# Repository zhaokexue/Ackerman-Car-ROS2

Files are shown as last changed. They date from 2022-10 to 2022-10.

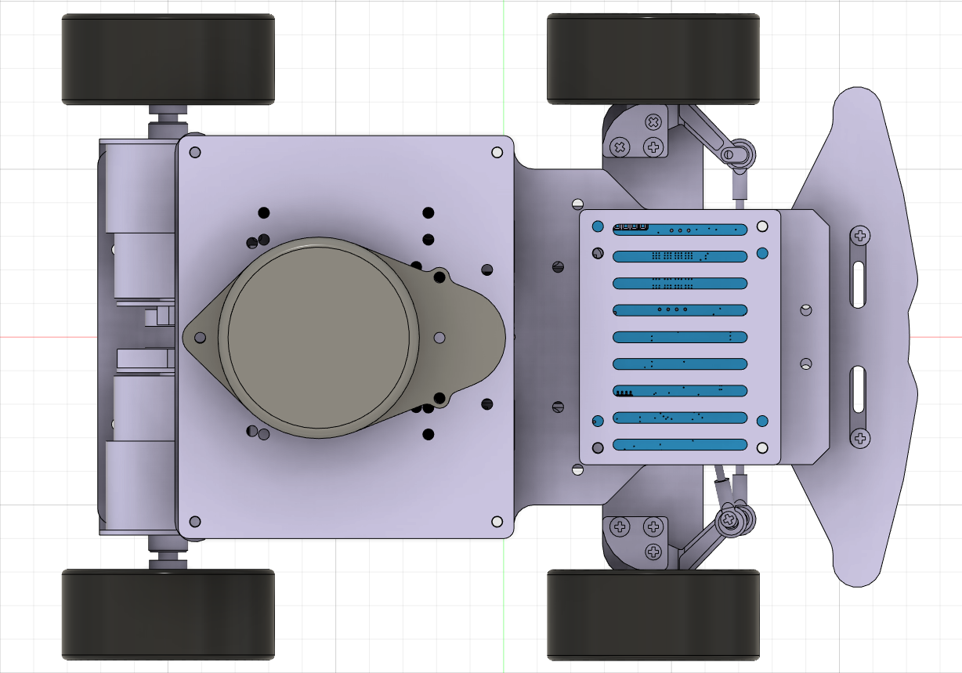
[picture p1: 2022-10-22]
1.阿克曼小车机械模型文件/屏幕截图 2022-10-22 131813.png

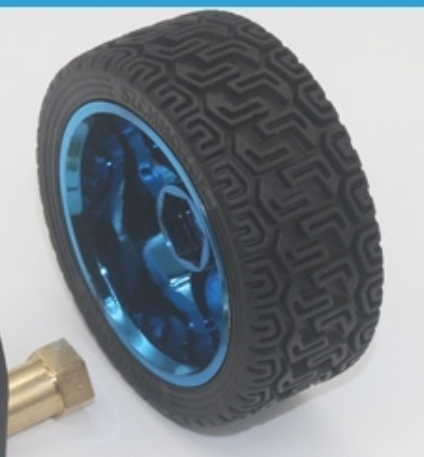
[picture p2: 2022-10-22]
3.搭建阿克曼小车材料准备/3.部分模块型号与图例/对应图片/12.png

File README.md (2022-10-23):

# ROS2阿克曼开发平台开源方案介绍

## 0、前言

### 0.1、项目背景：

为了满足更多的同学可以**快速**、**低成本**、**高兼容性**的搭建自己的阿克曼ROS2开发平台，所以出现本开源项目。

> 温馨提示：本次开源的硬件和软件是完全兼容差速和阿克曼方案的，也就是说你如果要做差速，更改机械部分之后，只需要改极少的配置文件就可以做到兼容。

开源项目发布方：**公众号：小白学移动机器人**

开源项目的内容：机械模型、底层驱动板PCB、底层驱动程序、ROS2部分功能包（启动功能包，描述功能包）等等

开源项目github地址获取：在公众号小白学移动机器人，发送：**ROS2阿克曼**，即可获取。

项目文件结构如下：



### 0.2、开源项目的总体方案：



### 0.3、开源项目的总体架构：



###0.4、开源项目的底层控制方案：



## 1、机械模型呈现

**详见：1.阿克曼小车机械模型文件**

这里机械板材的设计做了高兼容性：

> 1. 核心板安装兼容：树莓派、香橙派3LTS、jetson nano
> 2. 雷达兼容：RPLIDAR A1M8、乐动LD14、乐动LD19

左视图如下：



俯视图如下：



## 2、硬件方案介绍

详见：2.阿克曼小车硬件方案介绍

### 2.1、底层驱动板

**功能模块设计如下：**



**主控电路板PCB如下：**



**12V-5V 5A 电源板如下：**



### 2.2、核心板（香橙派3LTS）

开发板功能如下图：详见：官网：http://www.orangepi.cn/



## 3、底层驱动程序工程文件

详见：4.底层驱动程序工程文件

> 程序很简单，需要的同学可以自己看一下。
>
> 如果仍存在问题，可以参考我的系列博客文章解答你的问题。
>
> 博客链接：https://blog.csdn.net/zhao_ke_xue/article/details/108138981

博客详细的讲解的每一个控制模块的内容，如下所示：



**部分主流程代码如下：**

```c
#include "sys.h"

/*===================================================================
程序功能：ROS小车底层代码（全部） 差速底盘和阿克曼底盘通用
程序编写：公众号：小白学移动机器人
其他    ：如果对代码有任何疑问，可以私信小编，一定会回复的。
=====================================================================
------------------关注公众号，获得更多有趣的分享---------------------
===================================================================*/
int main(void)
{ 
	//发送计数
	char sendCount=0;
	
	GPIO_PinRemapConfig(GPIO_Remap_SWJ_Disable,ENABLE);
	GPIO_PinRemapConfig(GPIO_Remap_SWJ_JTAGDisable,ENABLE);//禁用JTAG 启用 SWD
	
	MY_NVIC_PriorityGroupConfig(2);	//=====设置中断分组
	
	delay_init();	    	        //=====延时函数初始化
	LED_Init();                     //=====LED初始化    程序灯	
	BEEP_Init();                    //=====蜂鸣器初始化，异常报警
	
	usart1_init(115200);	        //=====串口1初始化  树莓派通信
	usart3_init(115200);            //=====串口3初始化  蓝牙，控制和调试

	IIC_Init();                     //=====IIC初始化    读取MPU6050数据
	MPU6050_initialize();           //=====MPU6050初始化	
	DMP_Init();                     //=====初始化DMP 

	Encoder_Init_TIM3();            //=====初始化右轮编码器接口
	Encoder_Init_TIM4();            //=====初始化左轮编码器接口
	
	MY_ADC_Init();                  //=====adc初始化    电池电量检测
	
	Motor_PWM_Init(7200-1, 1-1);    //=====初始化PWM 10KHZ(AT8870)，用于驱动电机 
	Steer_PWM_Init(60000-1, 24-1);  //=====初始化PWM 50HZ，用于驱动舵机

	PID_Init();                     //=====PID初始化
	
	MBOT_EXTI_Init();               //=====MPU6050 5ms定时中断初始化

	while(1)
	{
		//给树莓派发送速度，角度,这里速度已经乘以1000,角度(0.0-359.0)乘以50
		if(sendCount==0)//发送  14.4ms  发送一次数据 70Hz 左右
		{
			//发送需要一定的延时
			usartSendData(USART1,(short)leftSpeedNow,(short)rightSpeedNow,(short)(yaw*50),sendCtrlFlag);  //1ms
			//蓝牙调试时用，不调试注释
			// pcShow();                                                           //2.2ms单个float数据
			sendCount++;
		}
		else
		{
			sendCount++;
			if(sendCount==25)
				sendCount=0;
		}
		//获取角度		
		getAngle(&yaw,&yaw_acc_error);                                                     
	} 
}

//中断服务函数
void USART1_IRQHandler()
{
	if(USART_GetITStatus(USART1, USART_IT_RXNE) != RESET)
 	 {
		 USART_ClearITPendingBit(USART1,USART_IT_RXNE);//首先清除中断标志位
		 usartReceiveOneData(USART1,&leftSpeedSet,&rightSpeedSet,&frontAngleSet,&receCtrlFlag);
	 }
}
```

**中断主流程代码如下：**

```c
/**************************************************************************
函数功能：所有的控制代码都在这里面
          5ms定时中断由MPU6050的INT引脚触发		
**************************************************************************/
void EXTI9_5_IRQHandler(void) 
{                                                         
	EXTI_ClearITPendingBit(EXTI_Line8);                             //===清除LINE8线路挂起位		
	
	Led_Flash(200);                                                 //===LED闪烁，证明程序正常运行	
	
	yaw_acc_error += FIVE_MS_ERROR;								    //===yaw漂移误差累加
	
	Get_battery_volt_average(&Voltage,100);		                    //===电池电压测量，单位mv，100次取一次平均
	
	Get_Motor_Speed(&leftSpeedNow,&rightSpeedNow);                  //===获取左右轮子真实速度
	
	pid_Task_Letf.speedSet  = leftSpeedSet;	                        //===给速度设定值和实时值赋值
	pid_Task_Right.speedSet = rightSpeedSet;
	pid_Task_Letf.speedNow  = leftSpeedNow;
	pid_Task_Right.speedNow = rightSpeedNow;
	
	Pid_Ctrl(&motorLeft,&motorRight);                               //===执行PID控制函数
	Steer_Ctrl(frontAngleSet,&motorFrontSteer);                     //===执行舵机，差速小车无需修改完全兼容

	if(Turn_Off(Voltage) == 0)                                      //===如果电量异常低
	{	
		BEEP_Disable();                                             //===正常情况，蜂鸣器失能 
		Set_Pwm(motorLeft,motorRight,motorFrontSteer);              //===赋值给PWM寄存器 		
	} 	  
	else
	{
		BEEP_Flash(20);                                            	//===电量报警
	}
} 
```

## 4、机械模型转URDF模型文件

详见：5.机械模型转URDF模型文件介绍

**rviz显示如下图：**



## 5、阿克曼结构运动模型详解

详见：6.阿克曼结构运动模型详解





## 6、阿克曼ROS2相关功能包

详见：7.ROS2相应功能包

```bash
.
└── src
    ├── mbot_bringup        # 机器人启动功能包 和 底层单片机通信、发布里程计、tf、订阅控制话题
    ├── mbot_description    # 机器人描述功能包，机械模型转的urdf
    └── sllidar_ros2-humble # RPLIDAR A1M8 的ROS2驱动
```

程序很简单，需要的同学可以自己看一下。

## 7、系统配置以及功能包启动说明

详见：8.系统配置以及功能包启动



##  8、总结

如果你觉得本开源项目还不错，可以积极的分享到你的同学、朋友。

**如果你感觉，我的文章比较适合你，关注我，点个赞，给你不一样的惊喜。**





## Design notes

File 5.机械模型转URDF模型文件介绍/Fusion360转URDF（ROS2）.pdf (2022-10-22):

# Fusion360转URDF（ROS2）

# 1、建模部分

# 1.1、熟悉fusion的基本操作

## 熟练使用命名视图

## 熟练使用草图工具

## 熟练使用移动工具

## 熟练使用测量工具

## 快捷键：

## m：移动选中的实体 i：测量长度 e：拉伸选中的面 f：倒圆角（选中的边或者面）

## 建模步骤：草图 - > 实体创建（相关操作）-> 从实体转换零部件 -> 装配（建立零部件之间的链接关系）

# 1.2、转换URDF对模型的要求

## 1. 模型尽可能简单，若是机械模型，先把主体部分合并为一个大的实体 2. 装配时建立零部件链接关系要正确，不能使用快速链接

# 1.3、建模的步骤

## 建模步骤：草图 - > 实体创建（相关操作）-> 从实体转换零部件 -> 装配（建立零部件之间的链接关系）

## 草图创建：

## 1. 选择创建的面 2. 通过任意线、矩形框、圆形框、镜像等工具，设计草图 3. 完成草图

## 实体的创建：

## 1. 选择需要操作的草图的面 2. 可以通过拉伸、旋转等操作对选择的面进行操作 3. 点击确定，即可生成一个新的实体

## 零部件的创建：

## 1. 从实体创建零部件 2. 实体消失，生成零部件 3. 修改零部件名称；名称必须是英文或者拼音

## 反复以上操作完成所有零部件的创建

## 创建零部件之间的链接关系：

## 1. 快捷键j

## 2. 只允许使用链接，不能使用快速链接

## 链接关系创建完成后，保存，文件结构如下图所示。

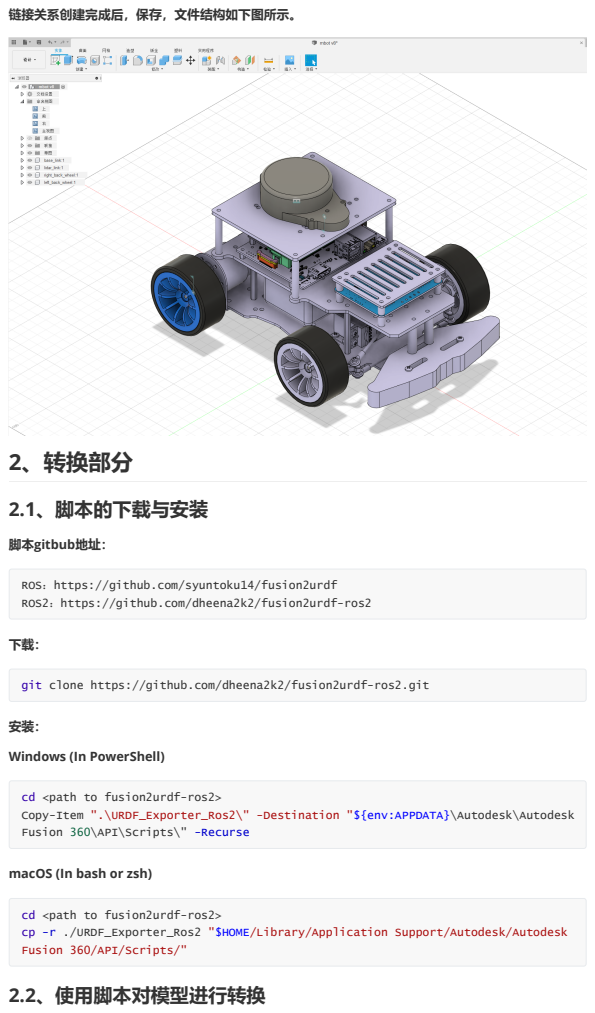
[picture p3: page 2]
2、转换部分; 2.1、脚本的下载与安装; 脚本gitbub地址：

ROS：https://github.com/syuntoku14/fusion2urdf
ROS2：https://github.com/dheena2k2/fusion2urdf-ros2

git clone https://github.com/dheena2k2/fusion2urdf-ros2.git

Windows (In PowerShell)

cd <path to fusion2urdf-ros2>
Copy-Item ".\URDF_Exporter_Ros2\" -Destination "${env:APPDATA}\Autodesk\Autodesk
Fusion 360\API\Scripts\" -Recurse

macOS (In bash or zsh)

cp -r ./URDF_Exporter_Ros2 "$HOME/Library/Application Support/Autodesk/Autodesk
Fusion 360/API/Scripts/"
2.2、使用脚本对模型进行转换

## 打开fusion360，点击实用程序、点击附加模块、选择我的脚本 URDF_Exporter_Ros2，最后点击运 行，选择生成文件夹。

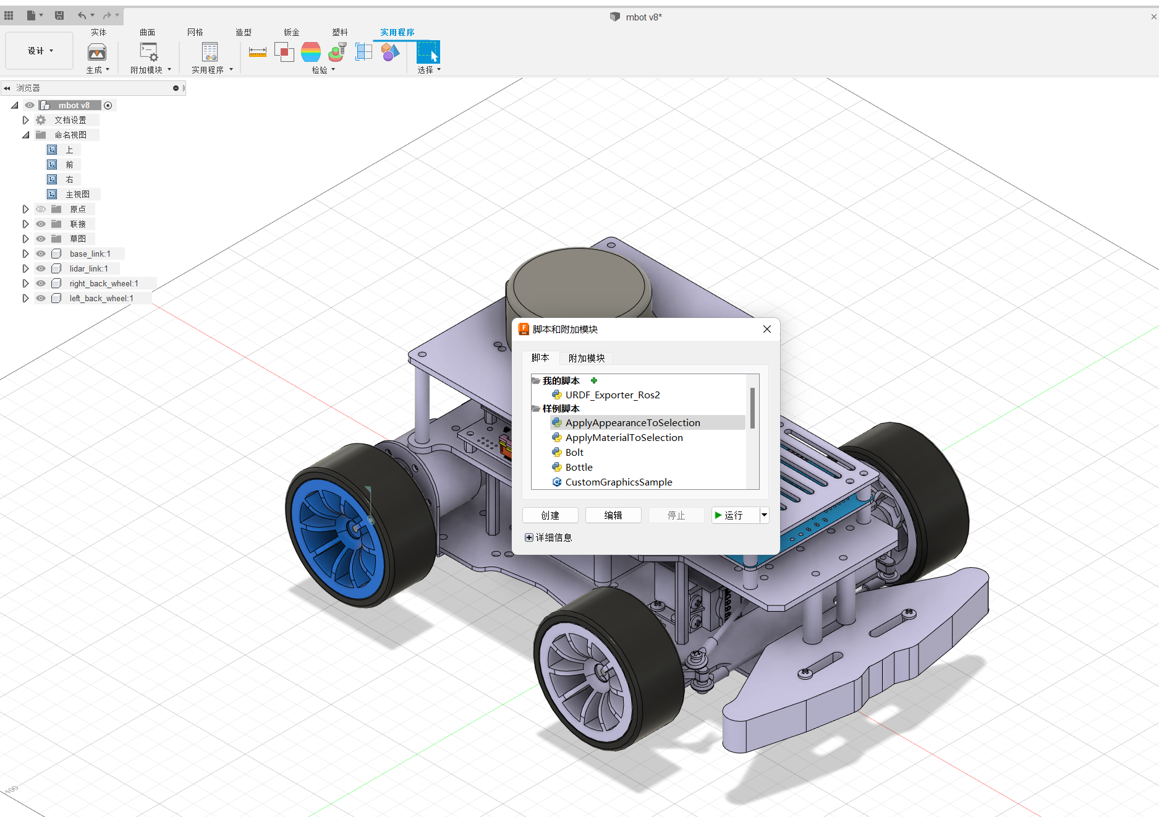
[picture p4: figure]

# 2.3、在ROS2使用转换后的ROS机器人描述功能包

## 首先，将生成的机器人描述功能包拷贝到ROS2的工作空间的src目录下

## ROS2环境与相关软件包安装：

## 编译与刷新环境：

## rviz显示运行：

sudo apt-get install libboost-dev #orangepi 没有安装此库 后期编译代码使用

ros2 launch mbot_description display.launch.py

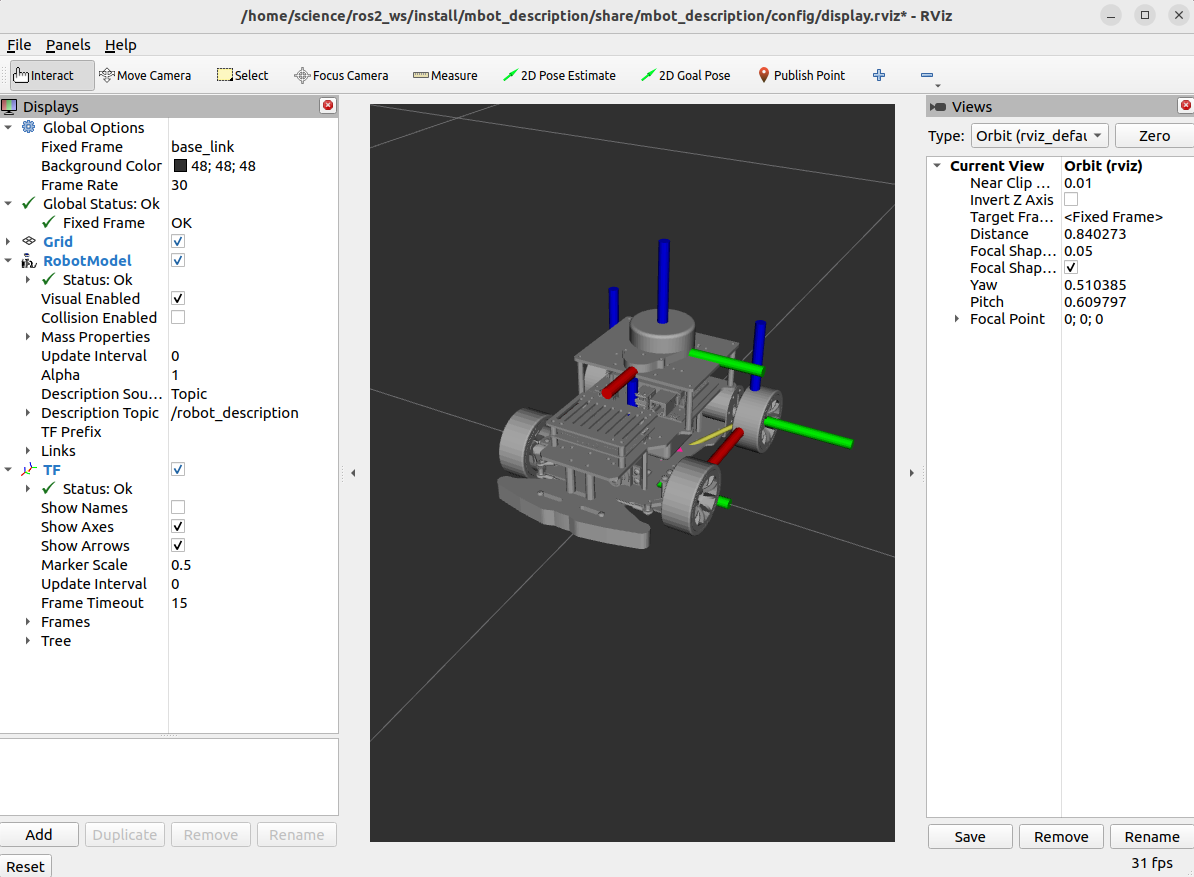
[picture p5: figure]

## 这样，通过fusion360建模软件就完成机器人描述文件的导出了。

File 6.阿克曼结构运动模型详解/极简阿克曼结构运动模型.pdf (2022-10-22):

# 极简版搭建阿克曼ROS小车相关

0、前言

## 本篇文章仅是对常见阿克曼ROS小车的极简分析，并提供代码。主要是方便读者自己搭建阿克曼小车时 理解使用。

## 这里仅针对《舵机控制前轮转向+后轮主动差速》的方式，如下图所示：

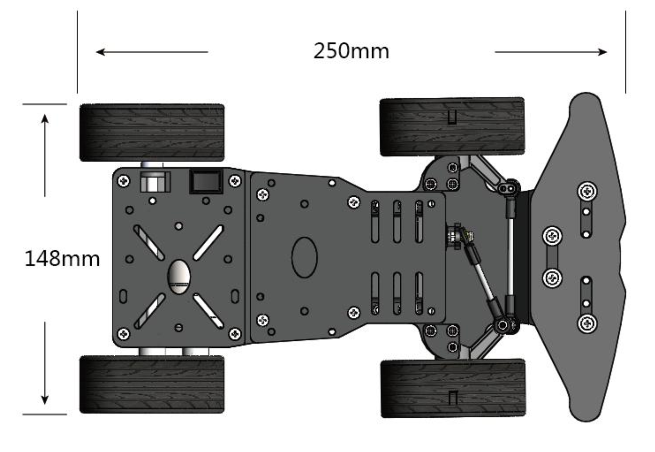
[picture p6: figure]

## 图片来源：百度图片

# 舵机转向机构简单示意图

## 舵机完成前轮的转向控制，简单示意图如下：

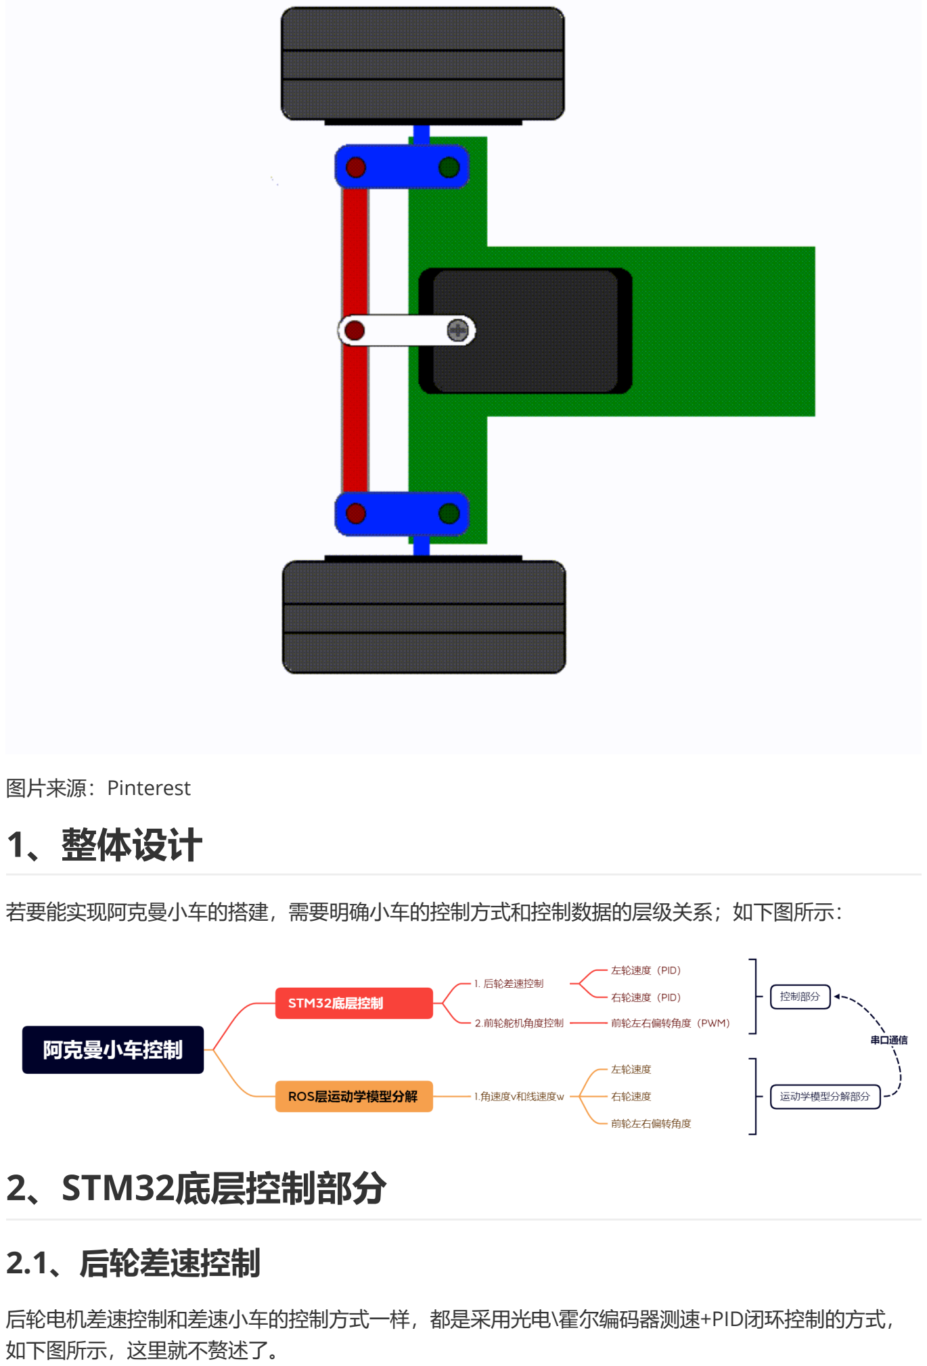
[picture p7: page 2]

## 图片来源：Pinterest

# 1、整体设计

## 若要能实现阿克曼小车的搭建，需要明确小车的控制方式和控制数据的层级关系；如下图所示：

# 2、STM32底层控制部分

# 2.1、后轮差速控制

## 后轮电机差速控制和差速小车的控制方式一样，都是采用光电\霍尔编码器测速+PID闭环控制的方式， 如下图所示，这里就不赘述了。

## 需要了解的朋友可以看之前的文章，链接如下：

# 2.2、前轮舵机角度控制

# 2.2.1、舵机选型：

## 这里主要使用如下两种模拟舵机，常见模拟舵机都可以。

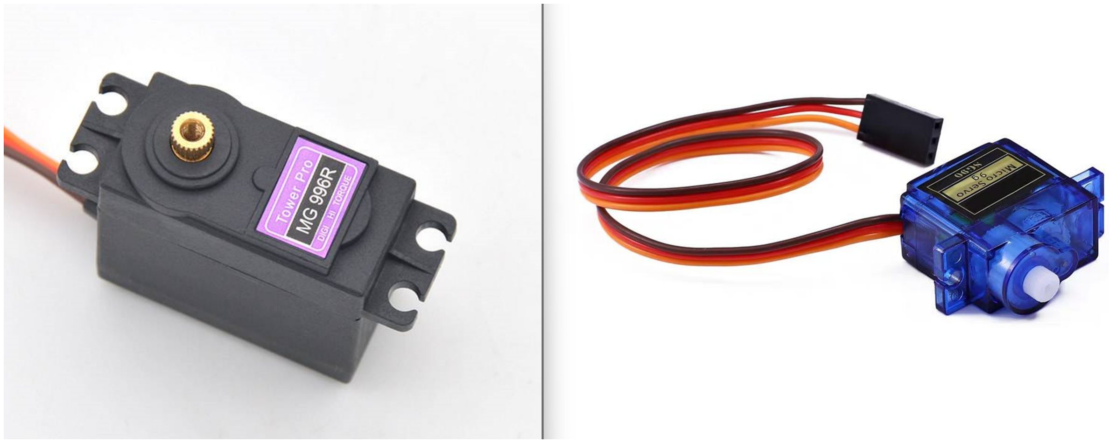
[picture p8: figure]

## 图片来源：百度图片

# 2.2.2、舵机控制原理：

## 舵机是一种位置伺服驱动器，是一种带有输出轴的小装置。当我们向伺服器发送一个控制信号时，输出 轴就可以转到特定的位置。只要在控制信号持续不变，伺服机构就会保持相对的角度位置不变。如果控 制信号发生变化，输出轴的位置也会相应发生变化。舵机的控制大部分都是通过PWM信号控制的。

# 2.2.3、单片机控制舵机：

## 模拟舵机控制一般需要20ms左右时基脉冲， 该脉冲高电平部分一般为0.5ms-2.5ms范围内角度控制脉 冲部分， 总间隔为2ms。 以180度角度伺服为例， 对应控制关系如下 ：

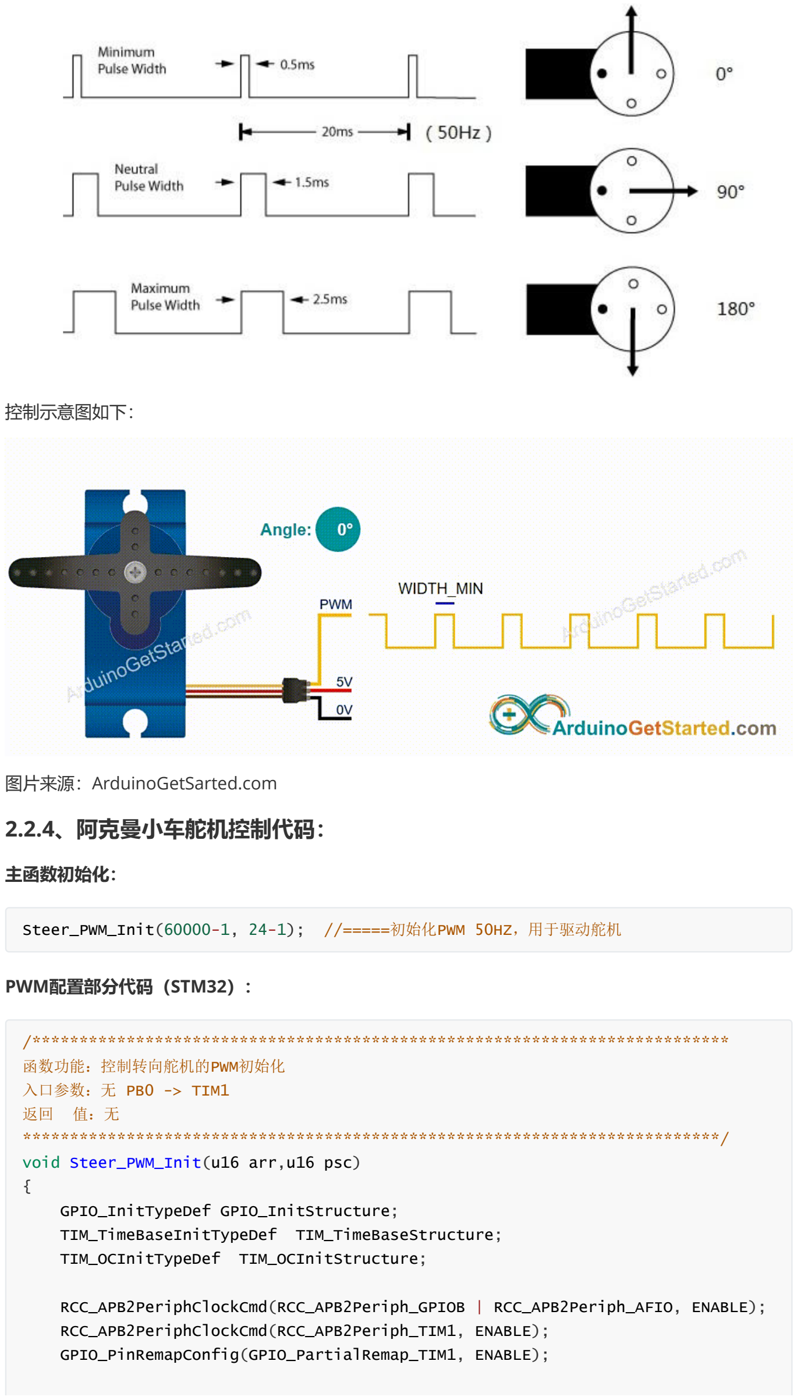
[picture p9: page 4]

## 控制示意图如下：

## 图片来源：ArduinoGetSarted.com

# 2.2.4、阿克曼小车舵机控制代码：

## 主函数初始化：

## PWM配置部分代码（STM32）：

Steer_PWM_Init(60000-1, 24-1); //=====初始化PWM 50HZ，用于驱动舵机

/************************************************************************** 函数功能：控制转向舵机的PWM初始化
入口参数：无 PB0 -> TIM1
返回 值：无
**************************************************************************/ void Steer_PWM_Init(u16 arr,u16 psc)
{
| GPIO_InitTypeDef GPIO_InitStructure; TIM_TimeBaseInitTypeDef TIM_TimeBaseStructure; TIM_OCInitTypeDef TIM_OCInitStructure;
| RCC_APB2PeriphClockCmd(RCC_APB2Periph_GPIOB | RCC_APB2Periph_AFIO, ENABLE); RCC_APB2PeriphClockCmd(RCC_APB2Periph_TIM1, ENABLE); GPIO_PinRemapConfig(GPIO_PartialRemap_TIM1, ENABLE);

## 前轮转向控制角度和PWM的转换函数：

GPIO_InitStructure.GPIO_Pin = GPIO_Pin_0; GPIO_InitStructure.GPIO_Mode = GPIO_Mode_AF_PP; GPIO_InitStructure.GPIO_Speed = GPIO_Speed_50MHz; GPIO_Init(GPIOB, &GPIO_InitStructure);

TIM_TimeBaseStructure.TIM_Period = arr; TIM_TimeBaseStructure.TIM_Prescaler = psc; TIM_TimeBaseStructure.TIM_ClockDivision = TIM_CKD_DIV1; TIM_TimeBaseStructure.TIM_CounterMode = TIM_CounterMode_Up; TIM_TimeBaseInit(TIM1, &TIM_TimeBaseStructure);

TIM_OCInitStructure.TIM_OCMode = TIM_OCMode_PWM1;
// * TIM1_CH2
// TIM_OCInitStructure.TIM_OutputState = TIM_OutputState_Enable; // TIM_OCInitStructure.TIM_Pulse = 0;
// TIM_OCInitStructure.TIM_OCPolarity = TIM_OCPolarity_High;
// * TIM1_CH2N
TIM_OCInitStructure.TIM_OutputNState = TIM_OutputNState_Enable; TIM_OCInitStructure.TIM_Pulse = 0; TIM_OCInitStructure.TIM_OCNPolarity = TIM_OCNPolarity_Low;
TIM_OC2Init(TIM1, &TIM_OCInitStructure); | //TIM_OC2
TIM_OC2PreloadConfig(TIM1, TIM_OCPreload_Enable);
TIM_ARRPreloadConfig(TIM1, ENABLE); | //使能TIMx在ARR上的预装载
寄存器
TIM_CtrlPWMOutputs(TIM1, ENABLE); | //MOE 主输出使能 | 高级定
时器使用

TIM_Cmd(TIM1, ENABLE);
}

//舵机PWM变量，初始安装为90度，注意机械安装时，要先转到90度再安装舵盘 int motorFrontSteer = 4500; // (60000 / 20ms) * 1.5ms = 4500 90度

//舵机控制角度的设定值
int frontAngleSet = 0;

// 物理结构限幅，舵机角度限幅
#define MAX_FRONT_ANGLE_SET (50)

/************************************************************************** 函数功能：舵机角度控制处理（SG90）角度线性变化
入口参数：ros端设定转向角度，需要给舵机的pwm，此处可根据不同的舵机自行更改
分辨率：1度 --> ((2.5ms - 0.5ms) / 180度) * (60000 / 20ms) = 33.3
0.5ms ------------------ 0度
1.5ms ------------------ 90度
2.5ms ------------------ 180度
返回 值：无
**************************************************************************/ void Steer_Ctrl(int frontAngleSet,int *motorFrontSteer)
{
| // 物理结构限幅 if(frontAngleSet > MAX_FRONT_ANGLE_SET)

{

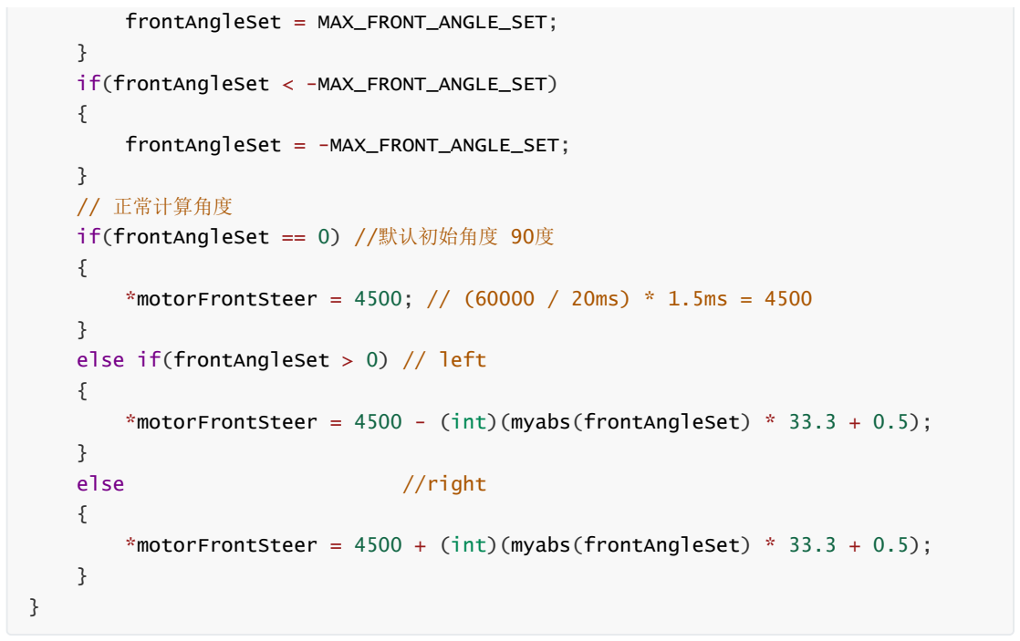
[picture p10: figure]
frontAngleSet = MAX_FRONT_ANGLE_SET;; } if(frontAngleSet < -MAX_FRONT_ANGLE_SET); frontAngleSet = -MAX_FRONT_ANGLE_SET;; } // 正常计算角度; if(frontAngleSet == 0) //默认初始角度 90度; } else if(frontAngleSet > 0) // left; else; //right

## 通过上面转换函数 Steer_Ctrl，我们可以将前轮转向角度准换为具体的PWM数值，剩下的部分就是 PWM设置的问题了，大家这么聪明，肯定不用我多说了。

大家是不是觉得阿克曼小车的底层控制部分 So Easy.

# 3、极简版阿克曼结构运动学模型

# 3.1、模型示意图介绍：

## 阿克曼底盘的运动学模型是一个全驱动模型，简化模型示意图如下：

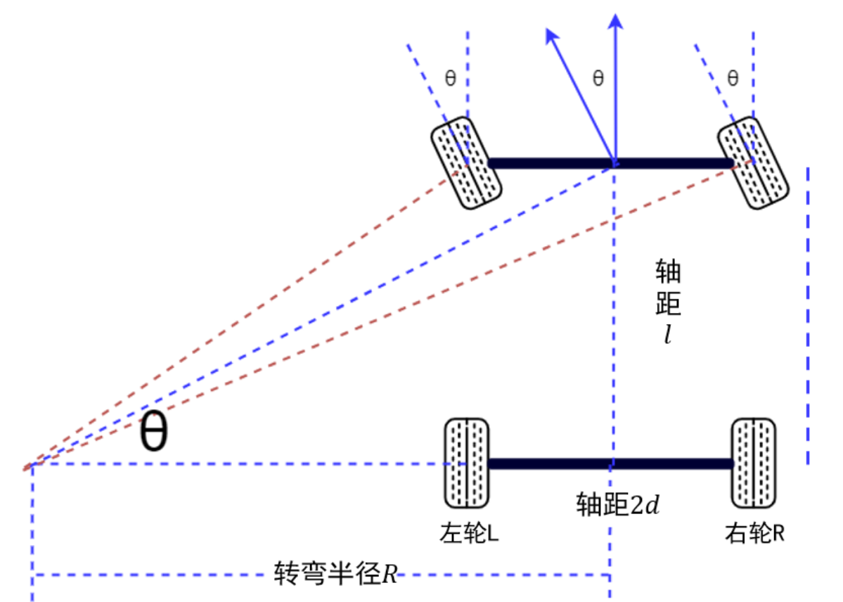
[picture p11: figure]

## 图片来源：CSDN：Jason.Li_0012 (https://blog.csdn.net/weixin_45929038)

*motorFrontSteer = 4500; // (60000 / 20ms) * 1.5ms = 4500

*motorFrontSteer = 4500 - (int)(myabs(frontAngleSet) * 33.3 + 0.5);

*motorFrontSteer = 4500 + (int)(myabs(frontAngleSet) * 33.3 + 0.5);

# 3.2、模型假设：

## 相对于理想的阿克曼底盘模型，这里为了简化模型，做了如下假设：

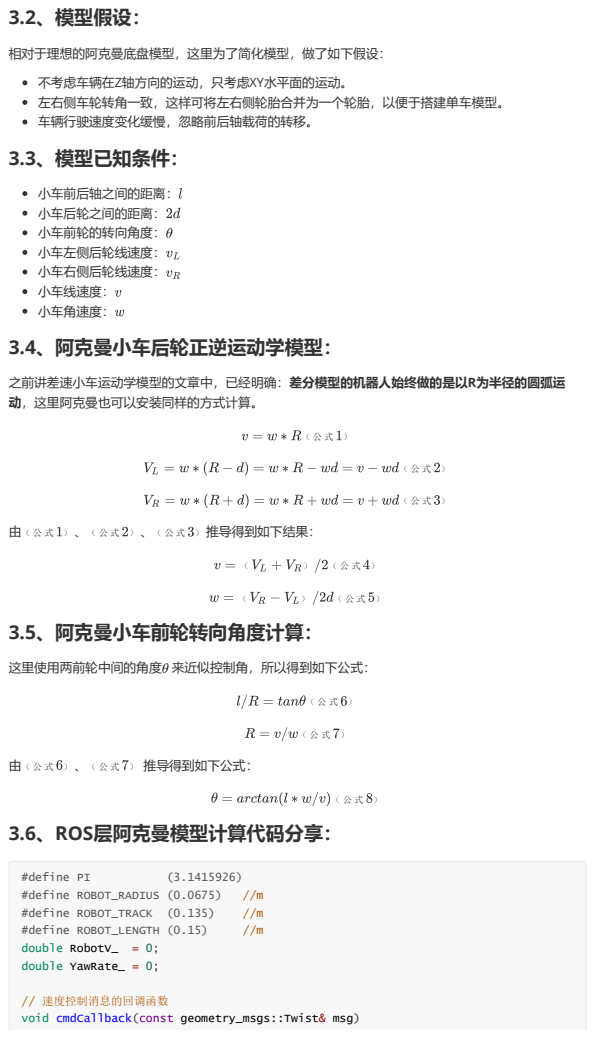
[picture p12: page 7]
小车前后轴之间的距离： 小车后轮之间的距离： 小车前轮的转向角度： 小车左侧后轮线速度： 小车右侧后轮线速度： 小车线速度： 小车角速度： 3.4、阿克曼小车后轮正逆运动学模型：; 由（ 公 式 ） 、（ 公 式 ） 、（ 公 式 ） 推导得到如下结果：; 3.5、阿克曼小车前轮转向角度计算：; 由（ 公 式 ） 、（ 公 式 ） 推导得到如下公式：; （ 公 式 ） 3.6、ROS层阿克曼模型计算代码分享：; #define PI; #define ROBOT_RADIUS (0.0675); #define ROBOT_TRACK; #define ROBOT_LENGTH (0.15); double RobotV_; double YawRate_ = 0;

不考虑车辆在Z轴方向的运动，只考虑XY水平面的运动。
左右侧车轮转角一致，这样可将左右侧轮胎合并为一个轮胎，以便于搭建单车模型。
车辆行驶速度变化缓慢，忽略前后轴载荷的转移。
3.3、模型已知条件：

之前讲差速小车运动学模型的文章中，已经明确：差分模型的机器人始终做的是以R为半径的圆弧运
动，这里阿克曼也可以安装同样的方式计算。

这里使用两前轮中间的角度 来近似控制角，所以得到如下公式：

// 速度控制消息的回调函数
void cmdCallback(const geometry_msgs::Twist& msg)

4、总结

## 如果你已经仔细的看到这里，那么恭喜你，你心中一定有了搭建阿克曼小车的控制思路了。

## 如果还没有理解，一定多看两遍。

## 偷偷的告诉大家，近期，我准备开源一整套，完整的ROS小车方案，包含差速小车和阿克曼小车，届时 将给大家提供完整上位机和下位机的代码，整套方案成本极低，千元以内。

## 下面是底层硬件方案，提前透露给大家。

{
RobotV_ | = msg.linear.x; | //m/s
YawRate_ = msg.angular.z; //rad/s
}

void Mbot::ackerCar(const double RobotV,const double YawRate) {
double r = RobotV / YawRate; // m
if(RobotV == 0) | // ackermann car can't trun rotation
{
sendLeftSpeed_ = 0;
sendRightSpeed_ = 0;
sendFrontAngle_ = 0;
}
else
if(YawRate == 0) // Pure forward/backward motion
{
sendLeftSpeed_ = (short)(RobotV * 1000.0);//mm/s sendRightSpeed_ = (short)(RobotV * 1000.0); sendFrontAngle_ = 0;
}
else | // Rotation about a point in space
{
sendLeftSpeed_ = (short)(YawRate * 1000.0 * (r - ROBOT_RADIUS));//mm/s sendRightSpeed_ = (short)(YawRate * 1000.0 * (r + ROBOT_RADIUS));

// 阿克曼约束一：后左右车轮转动需同向
if(RobotV > 0)
{
if(sendLeftSpeed_ < 0) {sendLeftSpeed_ = 0;} if(sendRightSpeed_ < 0) {sendRightSpeed_ = 0;} }
else if(RobotV < 0)
{
if(sendLeftSpeed_ > 0) {sendLeftSpeed_ = 0;}
if(sendRightSpeed_ > 0) {sendRightSpeed_ = 0;}
}
sendFrontAngle_ = atan(ROBOT_LENGTH * YawRate / RobotV ) * (180.0 / PI); // Deg
}
}

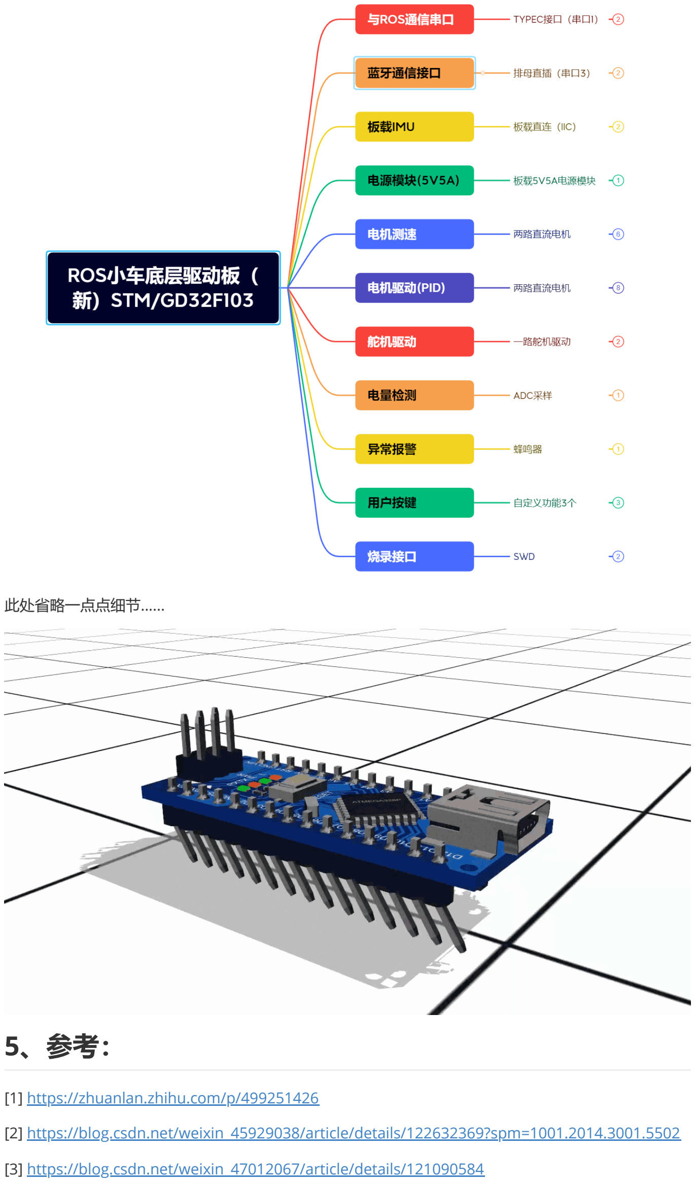
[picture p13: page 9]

此处省略一点点细节......

5、参考：

## [1] https://zhuanlan.zhihu.com/p/499251426

[2] https://blog.csdn.net/weixin_45929038/article/details/122632369?spm=1001.2014.3001.5502

## [3] https://blog.csdn.net/weixin_47012067/article/details/121090584

## [4] https://blog.csdn.net/honorzoey/article/details/113407979

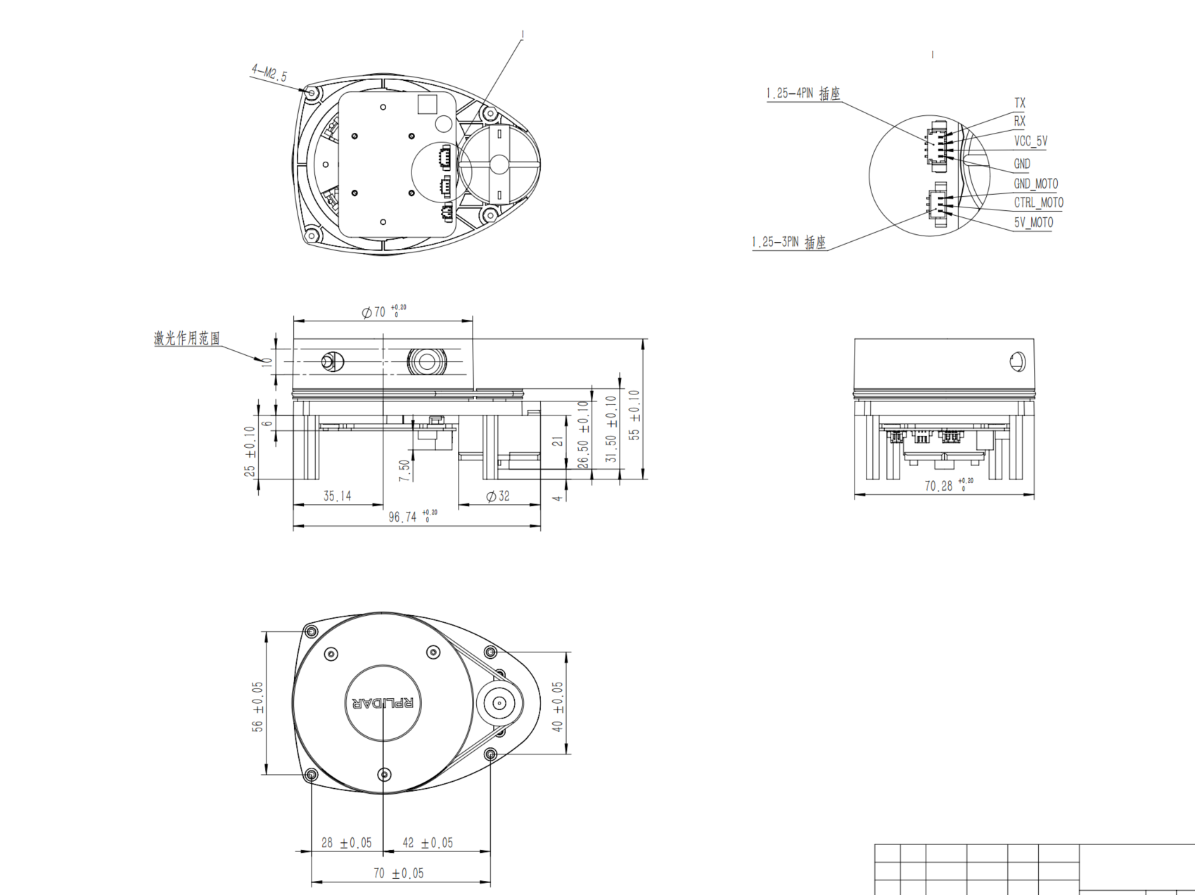
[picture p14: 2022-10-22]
2.阿克曼小车硬件方案介绍/3.RPLIADR A1M8/激光雷达-rplidar-A1M8.png

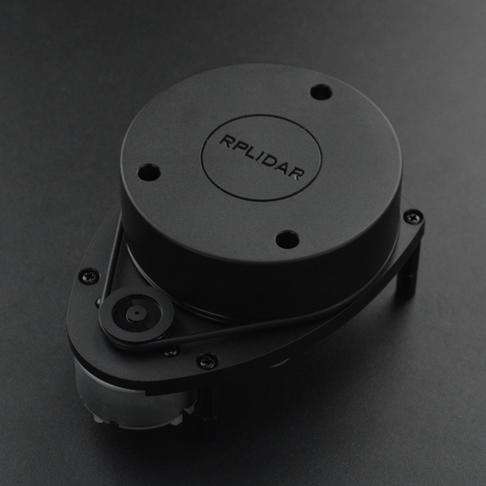
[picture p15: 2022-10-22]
2.阿克曼小车硬件方案介绍/3.RPLIADR A1M8/A1M8.jpeg

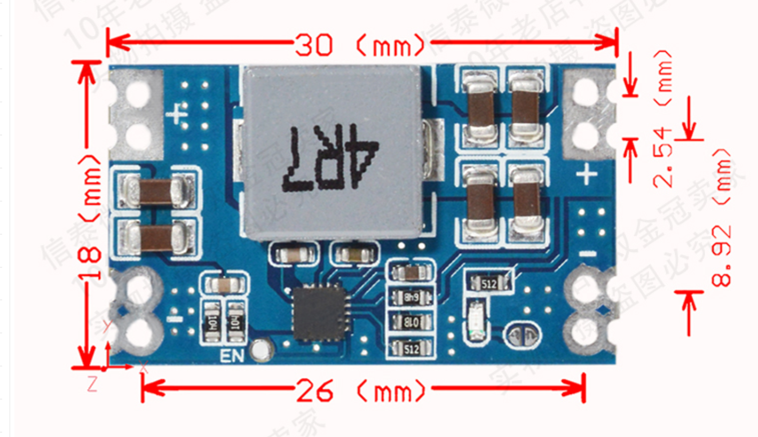
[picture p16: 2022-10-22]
2.阿克曼小车硬件方案介绍/1.STM32底层电路驱动板/3.电源板图（购买mini 560 12V-5V 5A）.png

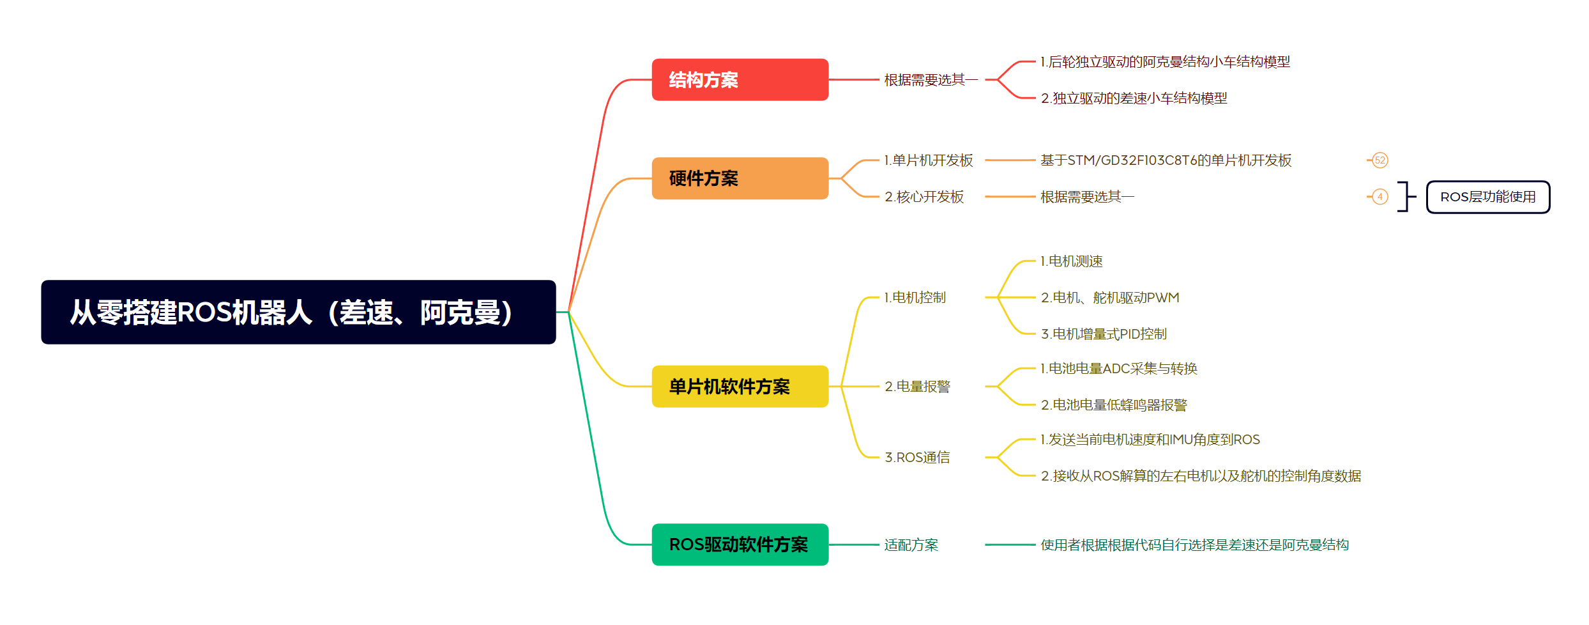
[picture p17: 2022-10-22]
0.开源项目介绍/差速/总体方案.png

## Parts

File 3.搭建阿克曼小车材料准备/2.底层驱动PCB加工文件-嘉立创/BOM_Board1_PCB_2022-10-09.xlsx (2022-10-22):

No. | Quantity | Comment | Designator | Footprint | Value | Manufacturer Part | Manufacturer | Supplier Part | Supplier
2 | 5 | 100n | C3,C21,C22,C23,C24 | C0402
3 | 7 | 0.1u | C6,C7,C12,C19,C20,C25,C33 | C0402
5 | 2 | 1u | C11,C13 | C0402
6 | 6 | 0.1u | C15,C28,C29,C30,C31,C32 | C1206
8 | 1 | 2.2n | C26 | C0805
9 | 1 | 100uF | C36 | CAP-SMD_BD8.0-L8.3-W8.3-LS9.3-FD | 100uF | RVT100UF50V67RV0040 | KNSCHA(科尼盛) | C2836439 | LCSC
10 | 2 | 22pF | C38,C39 | C0402 | 22pF | 0402CG220J500NT | FH(风华) | C1555 | LCSC
11 | 1 | 100uF | C40 | C1206 | 100uF | CL31A107MQHNNNE | SAMSUNG(三星) | C15008 | LCSC
14 | 1 | 0.35,0.75A | F1 | F0805 |  | 贴片保险丝0.05ASelf-recovery | RUILON | C30198 | LCSC
19 | 1 | 19-217/GHC-YR1S2/3T | LED1 | LED0603-R-RD |  | 19-217/GHC-YR1S2/3T | EVERLIGHT(台湾亿光) | C72043 | LCSC
20 | 1 | KT-0603R | LED2 | LED0603-R-RD |  | KT-0603R | KENTO | C2286 | LCSC
22 | 2 | 100K | R4,R15 | R0402
23 | 1 | 20K | R5 | R0402
25 | 4 | 4.7k | R12,R13,R14,R16 | R0402
27 | 1 | K2-1806SA-A3DW-04 | S1 | KEY-SMD_K2-1806SA-AXXW-XX
30 | 3 | K2-1806SA-A3DW-04 | SW1,SW2,SW3 | KEY-SMD_K2-1806SA-AXXW-XX |  | K2-1806SA-A3DW-04 | 韩国韩荣 | C2690015 | LCSC
34 | 1 | RT9013-33GB | U5 | SOT-23-5_L3.0-W1.7-P0.95-LS2.8-BR |  | RT9013-33GB | RICHTEK | C47773 | LCSC
40 | 1 | 8MHz | X1 | CRYSTAL-SMD_L5.0-W3.2 | 8MHz | X50328MSB2GI | YXC扬兴科技 | C115962 | LCSC
41 | 1 | 1k | R9 | R0402
42 | 4 | 10k | R6,R22,R23,R24 | R0402
43 | 1 | 510 | R8 | R0402
46 | 1 | 47 | R17 | R0402
47 | 2 | 0.2 | R25,R26 | R0805
48 | 1 | MMS8050-H-TP | Q3 | SOT-23-3_L2.9-W1.3-P1.90-LS2.4-BR
51 | 1 | TYPEC-307DSW-ACP16 | USB1 | USB-C-SMD_TYPEC-307DSW-ACP16
52 | 1 | C2765187 | USB3 | MICRO-USB-SMD_MICRO-5.9ZB5.0-040
53 | 1 | 1.5-4P卧贴 | H5 | CONN-SMD_ZH1.5-4P_SMD
54 | 1 | CH340N | U4 | SOP-8_L5.0-W4.0-P1.27-LS6.0-BL
55 | 1 | GD32F103C8T6 | U3 | TQFP-48_L7.0-W7.0-P0.50-LS9.0-BL
56 | 2 | AT8870 | U10、U11 | SOP-8_L4.9-W3.9-P1.27-LS6.0-BL-EP

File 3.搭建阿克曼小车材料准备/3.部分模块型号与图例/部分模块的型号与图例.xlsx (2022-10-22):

序号 | 名称 | 型号 | 个数 | 淘宝链接
1 | SD卡 | 闪迪8\16G高速卡 | 1 | https://item.taobao.com/item.htm?spm=a1z09.2.0.0.5a282e8d9ynWcl&id=648729260877&_u=n27e0jt0e6f9
2 | 电池套装 | 12V电池充电器套装 | 1 | https://item.taobao.com/item.htm?spm=a1z09.2.0.0.5a282e8d9ynWcl&id=624879497879&_u=n27e0jt0d620
3 | XT30U电池插头连接线 | 母头10cm | 1 | https://item.taobao.com/item.htm?spm=a1z09.2.0.0.5a282e8d9ynWcl&id=598407253999&_u=n27e0jt0d5d5
4 | USB转安卓micro | 15cm 数据线 | 1 | https://detail.tmall.com/item.htm?_u=n27e0jt0f0cd&id=646439713283&spm=a1z09.2.0.0.5a282e8d9ynWcl
5 | USB转TYPEC | 25cm 数据线 | 1 | https://detail.tmall.com/item.htm?_u=n27e0jt09f1e&id=666724356790&spm=a1z09.2.0.0.5a282e8d9ynWcl
6 | 安卓micro转TYPEC | 25cm 数据线 | 1 | https://item.taobao.com/item.htm?spm=a1z09.2.0.0.5a282e8d9ynWcl&id=652595705306&_u=n27e0jt0b8d3
7 | 底层板需要的一些配件 | 底层驱动板需要的 | 1 | https://item.taobao.com/item.htm?spm=a1z09.2.0.0.5a282e8d9ynWcl&id=635227665423&_u=n27e0jt04848
8 | 亚克力加工 |  | 1 | https://item.taobao.com/item.htm?spm=a1z09.2.0.0.5a282e8d9ynWcl&id=650568186676&_u=n27e0jt0e97c
9 | 舵机 | MG995 | 1 | https://item.taobao.com/item.htm?spm=a1z09.2.0.0.5a282e8d9ynWcl&id=573547711366&_u=n27e0jt045a3
10 | 舵机座 | 配件MG995 | 1 | https://item.taobao.com/item.htm?spm=a1z09.2.0.0.5a282e8d9ynWcl&id=603661493122&_u=n27e0jt054bd
11 | 前轮舵机转向结构 |  | 1 | https://item.taobao.com/item.htm?spm=a1z09.2.0.0.5a282e8d9ynWcl&id=656136453494&_u=n27e0jt0a753
12 | 智能小车轮子 | 防滑车轮 | 2 | https://item.taobao.com/item.htm?spm=a1z09.2.0.0.5a282e8d9ynWcl&id=656136453494&_u=n27e0jt0a753
13 | 12V直流减速电机 | 12V直流减速电机套装 | 2 | https://item.taobao.com/item.htm?spm=a1z0d.6639537/tb.1997196601.312.48c77484EUyhPv&id=584588142034
14 | 香橙派 | 3LTS | 1 | https://item.taobao.com/item.htm?spm=a1z0d.6639537/tb.1997196601.389.48c77484EUyhPv&id=665424457812
15 | 电机链接线 | H2.54排线-6p-25cm | 2 | https://item.taobao.com/item.htm?spm=a1z10.3-c-s.w4002-21223910208.14.2a696a4bWT919G&id=565759164574

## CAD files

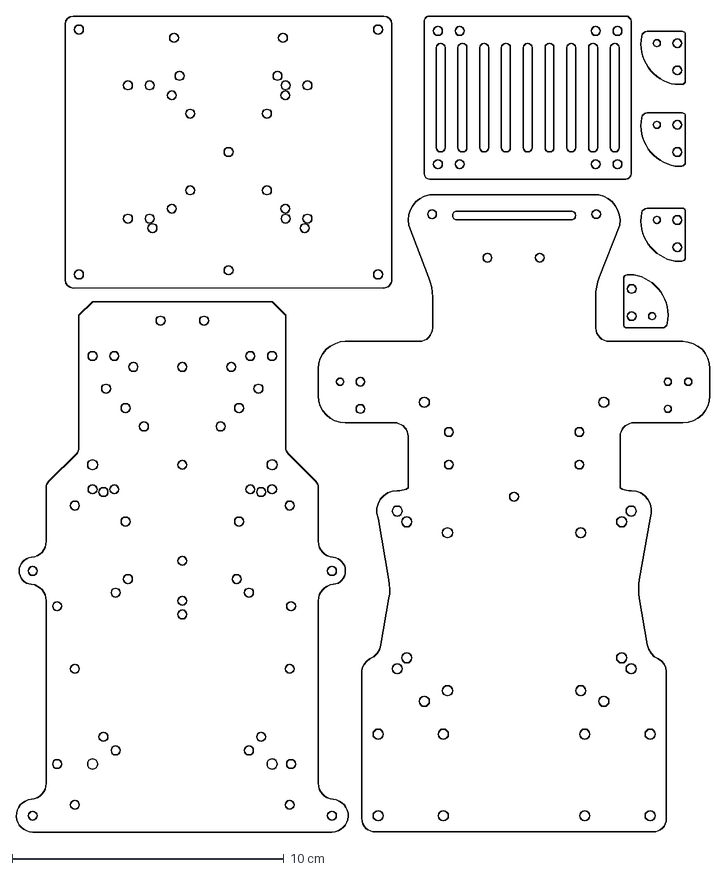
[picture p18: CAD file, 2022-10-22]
3.搭建阿克曼小车材料准备/1.阿克曼小车机械主体板材加工文件 - 淘宝亚克力定制加工/mbot_v2.dxf
25.5 x 30.0 cm

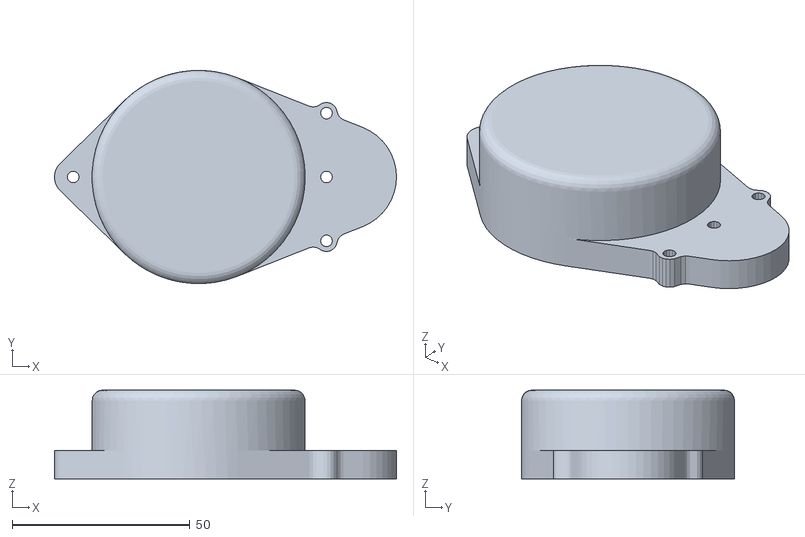
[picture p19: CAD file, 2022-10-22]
7.ROS2相应功能包/mbot_description/meshes/lidar_link_1.stl
96.3 x 60.0 x 25.0

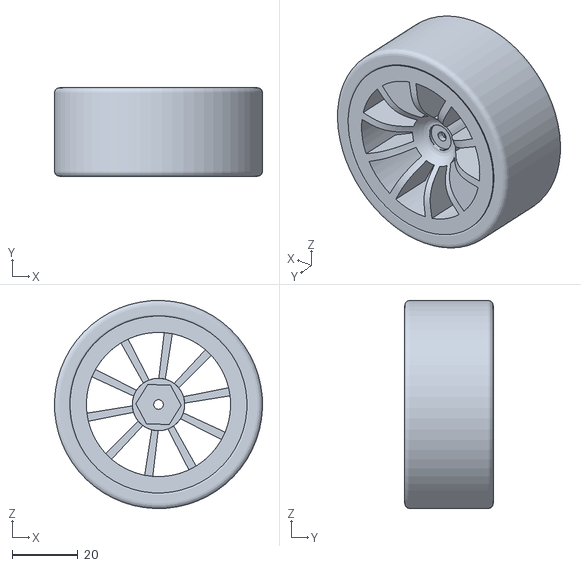
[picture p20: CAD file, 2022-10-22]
7.ROS2相应功能包/mbot_description/meshes/left_back_wheel_1.stl
63.4 x 27.0 x 63.4

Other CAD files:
7.ROS2相应功能包/mbot_description/meshes/right_back_wheel_1.stl

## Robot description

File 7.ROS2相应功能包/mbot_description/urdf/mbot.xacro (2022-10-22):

<?xml version="1.0" ?>
<robot name="mbot" xmlns:xacro="http://www.ros.org/wiki/xacro">

<xacro:include filename="$(find mbot_description)/urdf/materials.xacro" />
<xacro:include filename="$(find mbot_description)/urdf/mbot.trans" />
<xacro:include filename="$(find mbot_description)/urdf/mbot.gazebo" />
<link name="base_link">
  <inertial>
    <origin xyz="-0.007078599561218432 1.9724380014176952e-05 0.04251572924254428" rpy="0 0 0"/>
    <mass value="5.464337682688795"/>
    <inertia ixx="0.014973" iyy="0.027123" izz="0.035321" ixy="-2.4e-05" iyz="1e-06" ixz="0.002181"/>
  </inertial>
  <visual>
    <origin xyz="0 0 0" rpy="0 0 0"/>
    <geometry>
      <mesh filename="file://$(find mbot_description)/meshes/base_link.stl" scale="0.001 0.001 0.001"/>
    </geometry>
    <material name="silver"/>
  </visual>
  <collision>
    <origin xyz="0 0 0" rpy="0 0 0"/>
    <geometry>
      <mesh filename="file://$(find mbot_description)/meshes/base_link.stl" scale="0.001 0.001 0.001"/>
    </geometry>
  </collision>
</link>

<link name="right_back_wheel">
  <inertial>
    <origin xyz="-1.6533433490339977e-07 -0.00647885642709535 5.119932255936988e-13" rpy="0 0 0"/>
    <mass value="0.2490929871526092"/>
    <inertia ixx="9.3e-05" iyy="0.000155" izz="9.3e-05" ixy="-0.0" iyz="0.0" ixz="0.0"/>
  </inertial>
  <visual>
    <origin xyz="0.099924 0.077 -0.0315" rpy="0 0 0"/>
    <geometry>
      <mesh filename="file://$(find mbot_description)/meshes/right_back_wheel_1.stl" scale="0.001 0.001 0.001"/>
    </geometry>
    <material name="silver"/>
  </visual>
  <collision>
    <origin xyz="0.099924 0.077 -0.0315" rpy="0 0 0"/>
    <geometry>
      <mesh filename="file://$(find mbot_description)/meshes/right_back_wheel_1.stl" scale="0.001 0.001 0.001"/>
    </geometry>
  </collision>
</link>

<link name="left_back_wheel">
  <inertial>
    <origin xyz="-1.6533495193760128e-07 0.0064791947454798104 6.172562461159714e-13" rpy="0 0 0"/>
    <mass value="0.24909336875248736"/>
    <inertia ixx="9.3e-05" iyy="0.000155" izz="9.3e-05" ixy="-0.0" iyz="-0.0" ixz="0.0"/>
  </inertial>
  <visual>
    <origin xyz="0.099924 -0.077 -0.0315" rpy="0 0 0"/>
    <geometry>
      <mesh filename="file://$(find mbot_description)/meshes/left_back_wheel_1.stl" scale="0.001 0.001 0.001"/>
    </geometry>
    <material name="silver"/>
  </visual>
  <collision>
    <origin xyz="0.099924 -0.077 -0.0315" rpy="0 0 0"/>
    <geometry>
      <mesh filename="file://$(find mbot_description)/meshes/left_back_wheel_1.stl" scale="0.001 0.001 0.001"/>
    </geometry>
  </collision>
</link>

<link name="lidar_link">
  <inertial>
    <origin xyz="0.002881471612091506 1.653346680917725e-07 0.011508813813586163" rpy="0 0 0"/>
    <mass value="0.620567666884242"/>
    <inertia ixx="0.000165" iyy="0.000252" izz="0.000351" ixy="-0.0" iyz="-0.0" ixz="1.3e-05"/>
  </inertial>
  <visual>
    <origin xyz="0.055621 -0.0 -0.108" rpy="0 0 0"/>
    <geometry>
      <mesh filename="file://$(find mbot_description)/meshes/lidar_link_1.stl" scale="0.001 0.001 0.001"/>
    </geometry>
    <material name="silver"/>
  </visual>
  <collision>
    <origin xyz="0.055621 -0.0 -0.108" rpy="0 0 0"/>
    <geometry>
      <mesh filename="file://$(find mbot_description)/meshes/lidar_link_1.stl" scale="0.001 0.001 0.001"/>
    </geometry>
  </collision>
</link>

<joint name="j1" type="continuous">
  <origin xyz="-0.099924 -0.077 0.0315" rpy="0 0 0"/>
  <parent link="base_link"/>
  <child link="right_back_wheel"/>
  <axis xyz="-0.0 -1.0 -0.0"/>
</joint>

<joint name="j2" type="continuous">
  <origin xyz="-0.099924 0.077 0.0315" rpy="0 0 0"/>
  <parent link="base_link"/>
  <child link="left_back_wheel"/>
  <axis xyz="0.0 1.0 -0.0"/>
</joint>

<joint name="g1" type="fixed">
  <origin xyz="-0.055621 0.0 0.108" rpy="0 0 0"/>
  <parent link="base_link"/>
  <child link="lidar_link"/>
</joint>

</robot>

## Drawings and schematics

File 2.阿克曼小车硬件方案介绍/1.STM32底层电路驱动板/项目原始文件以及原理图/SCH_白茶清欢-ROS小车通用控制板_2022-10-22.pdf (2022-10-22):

MCU | UART
IMU | BEEP

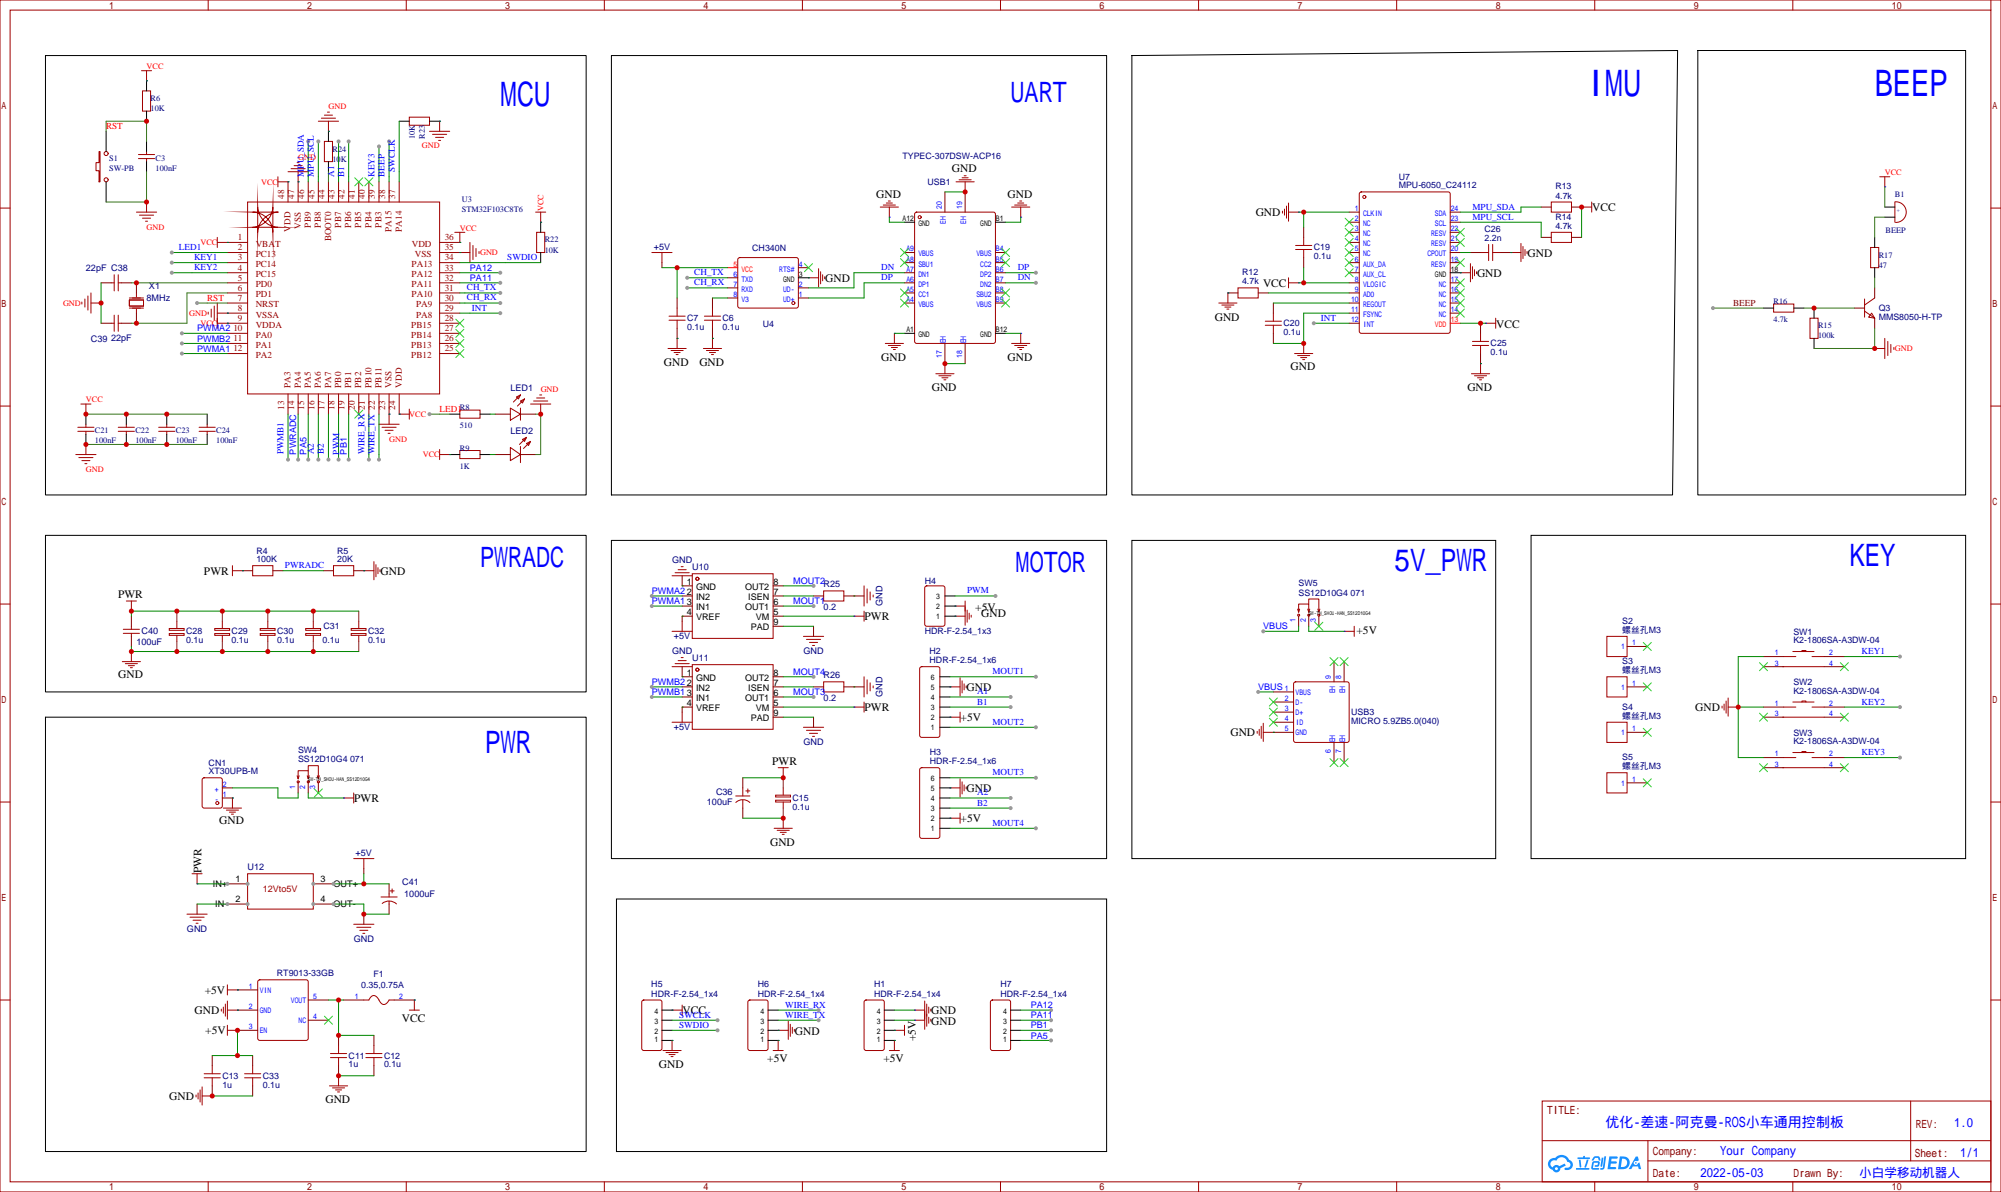
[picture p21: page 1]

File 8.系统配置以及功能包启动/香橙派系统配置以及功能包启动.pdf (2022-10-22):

# 香橙派系统配置以及功能包启动

# 1.系统镜像下载

## 1. 这里我们需要安装ROS2的humble版本，需要ubuntu 22.04版本的系统。

## 2. 香橙派镜像下载：http://www.orangepi.cn/html/hardWare/computerAndMicrocontrollers/ser

vice-and-support/Orange-Pi-3-LTS.html (http://www.orangepi.cn/html/hardWare/computerAndMicrocontrollers/service-and-support/Orange-Pi-3-LTS.html)

## 3. 点击Ubuntu镜像，选择jammy桌面版或者服务器版，如下图所示

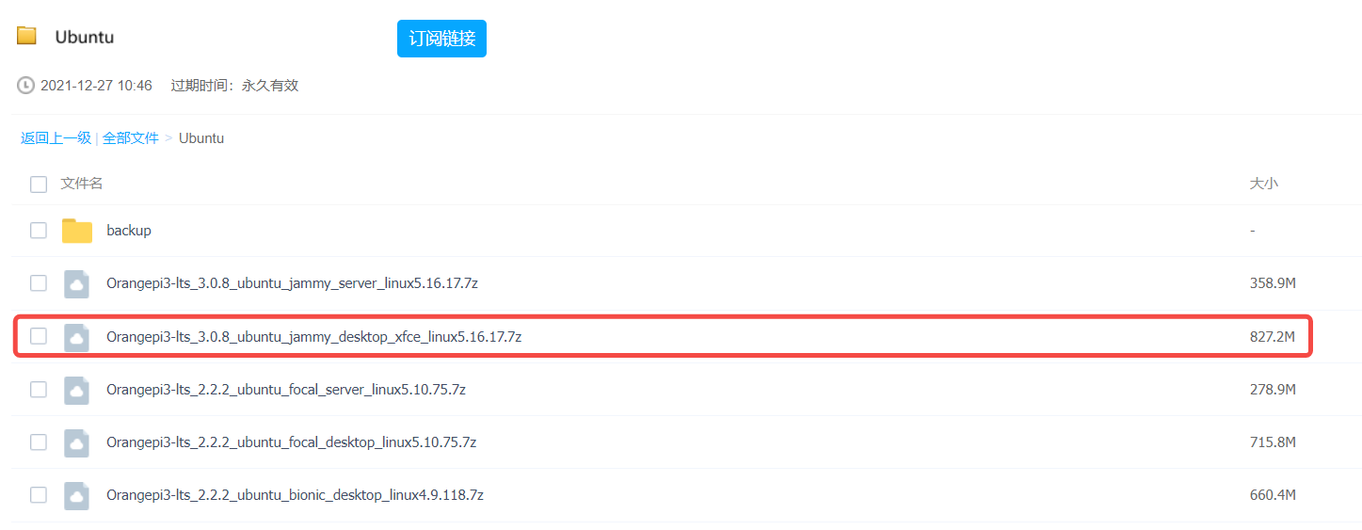
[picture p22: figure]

# 2.系统镜像安装

## 1. 插入读卡器，使用SD Card Formatter软件 格式化SD卡

## 2. 选好盘符，点击Format，点击弹窗确认，如下图所示：

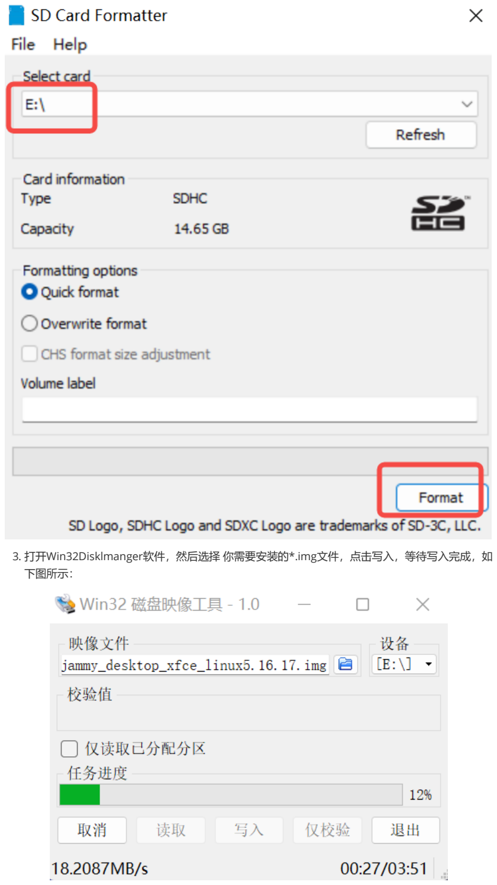
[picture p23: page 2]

## 3. 打开Win32Disklmanger软件，然后选择 你需要安装的*.img文件，点击写入，等待写入完成，如 下图所示：

# 3.配网以及xshell连接香橙派

## 1. 香橙派连接wifi，获得IP地址 2. 客户端和香橙派连接同一个局域网 3. 打开xshell，新建一个链接

## 4. 用户名：orangepi ，密码：orangepi

# 4.环境准备

# 0. 可通过配置选择关闭桌面版 （非必选）

sudo orangepi-config

# 1. ROS2安装

wget http://fishros.com/install -O fishros && . fishros # 1 、1、2、3、1、2

# 2. 安装键盘控制功能包

sudo apt-get install ros-humble-teleop-twist-keyboard

# 3. 安装机器人描述功能包需要使用的相关功能包

sudo apt-get install ros-humble-xacro
sudo apt-get install ros-humble-joint-state-publisher

# 4. 卸载brltty程序，防止ttyUSB端口被占用

sudo apt-get purge brltty # 删除端口占用

# 5. 安装boost，串口通信程序需要，香橙派版默认没有安装 sudo apt-get install libboost-dev

# 6. reboot，到这里环境就准备ok了。

reboot
## 若出现包更新错误

E: 读错误 - read (5: 输入/输出错误)
E: 无法解析或打开软件包的列表或是状态文件。

# 英文是：

E：Read error - read (5 Input/output error),
E:The package lists or status file could not be parsed or opened.

刚开始是以为分区有错，所以用ubuntu的启动盘运行fsck -f /dev/sdX，检查根目录分区，但是问题依 旧。

# 解决办法是：

sudo rm /var/lib/dpkg/status
sudo cp /var/lib/dpkg/status-old /var/lib/dpkg/status sudo rm -rf /var/lib/apt/lists/*

sudo apt-get update

# 问题解决。

# 5.阿克曼小车驱动功能包相关准备

## 1.打开一个终端，新建ROS2工作空间文件夹

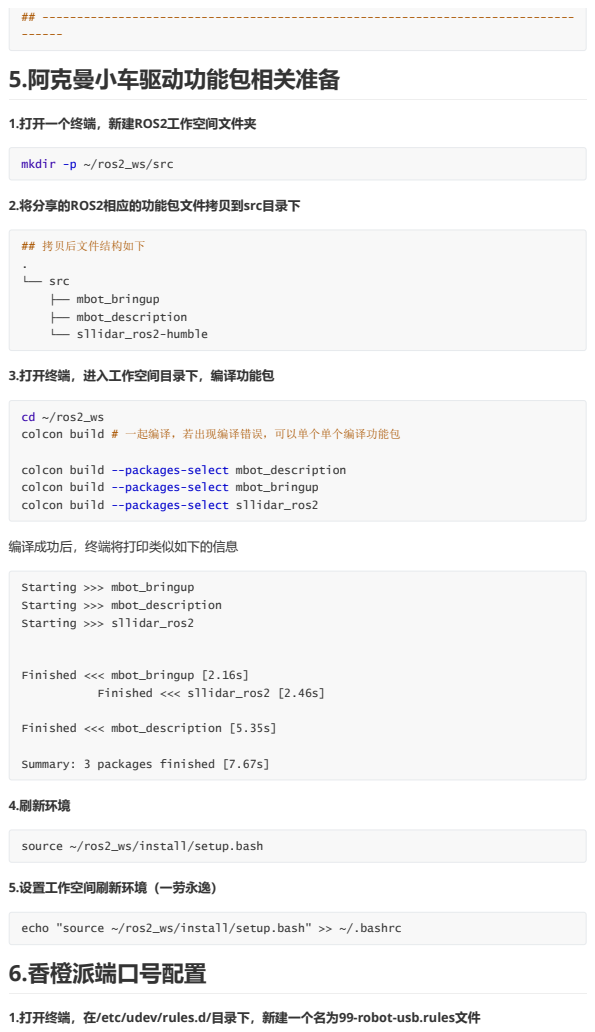
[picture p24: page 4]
2.将分享的ROS2相应的功能包文件拷贝到src目录下; 编译成功后，终端将打印类似如下的信息; 4.刷新环境; 5.设置工作空间刷新环境（一劳永逸）; mkdir -p ~/ros2_ws/src; ## 拷贝后文件结构如下; . └── src; ├── mbot_bringup; ├── mbot_description; └── sllidar_ros2-humble; Starting >>> mbot_bringup; Starting >>> mbot_description; Starting >>> sllidar_ros2; Finished <<< mbot_bringup [2.16s]; Finished <<< sllidar_ros2 [2.46s]; Finished <<< mbot_description [5.35s]

3.打开终端，进入工作空间目录下，编译功能包

cd ~/ros2_ws
colcon build # 一起编译，若出现编译错误，可以单个单个编译功能包

colcon build --packages-select mbot_description
colcon build --packages-select mbot_bringup
colcon build --packages-select sllidar_ros2

Summary: 3 packages finished [7.67s]

source ~/ros2_ws/install/setup.bash

echo "source ~/ros2_ws/install/setup.bash" >> ~/.bashrc
6.香橙派端口号配置

1.打开终端，在/etc/udev/rules.d/目录下，新建一个名为99-robot-usb.rules文件

## 2.将如下内容复制到文件中

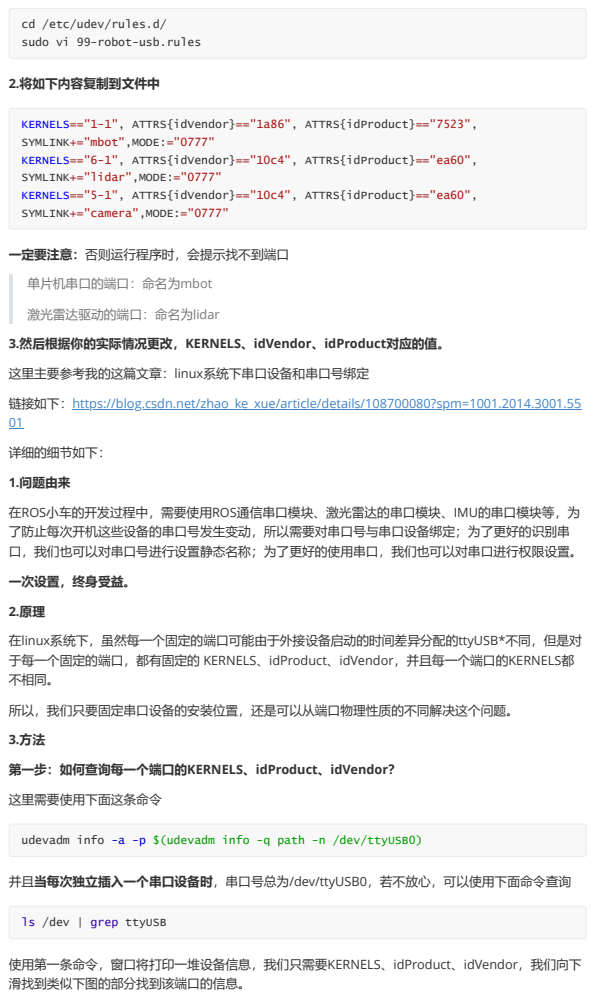
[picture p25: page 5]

cd /etc/udev/rules.d/
sudo vi 99-robot-usb.rules

KERNELS=="1-1", ATTRS{idVendor}=="1a86", ATTRS{idProduct}=="7523",
SYMLINK+="mbot",MODE:="0777"
KERNELS=="6-1", ATTRS{idVendor}=="10c4", ATTRS{idProduct}=="ea60",
SYMLINK+="lidar",MODE:="0777"
KERNELS=="5-1", ATTRS{idVendor}=="10c4", ATTRS{idProduct}=="ea60",
SYMLINK+="camera",MODE:="0777"

一定要注意：否则运行程序时，会提示找不到端口
单片机串口的端口：命名为mbot
激光雷达驱动的端口：命名为lidar
3.然后根据你的实际情况更改，KERNELS、idVendor、idProduct对应的值。
这里主要参考我的这篇文章：linux系统下串口设备和串口号绑定
链接如下：https://blog.csdn.net/zhao_ke_xue/article/details/108700080?spm=1001.2014.3001.55
详细的细节如下：
1.问题由来
在ROS小车的开发过程中，需要使用ROS通信串口模块、激光雷达的串口模块、IMU的串口模块等，为
了防止每次开机这些设备的串口号发生变动，所以需要对串口号与串口设备绑定；为了更好的识别串
口，我们也可以对串口号进行设置静态名称；为了更好的使用串口，我们也可以对串口进行权限设置。
一次设置，终身受益。
在linux系统下，虽然每一个固定的端口可能由于外接设备启动的时间差异分配的ttyUSB*不同，但是对
于每一个固定的端口，都有固定的 KERNELS、idProduct、idVendor，并且每一个端口的KERNELS都
不相同。
所以，我们只要固定串口设备的安装位置，还是可以从端口物理性质的不同解决这个问题。
第一步：如何查询每一个端口的KERNELS、idProduct、idVendor？
这里需要使用下面这条命令

udevadm info -a -p $(udevadm info -q path -n /dev/ttyUSB0)

并且当每次独立插入一个串口设备时，串口号总为/dev/ttyUSB0，若不放心，可以使用下面命令查询

ls /dev | grep ttyUSB

使用第一条命令，窗口将打印一堆设备信息，我们只需要KERNELS、idProduct、idVendor，我们向下
滑找到类似下图的部分找到该端口的信息。

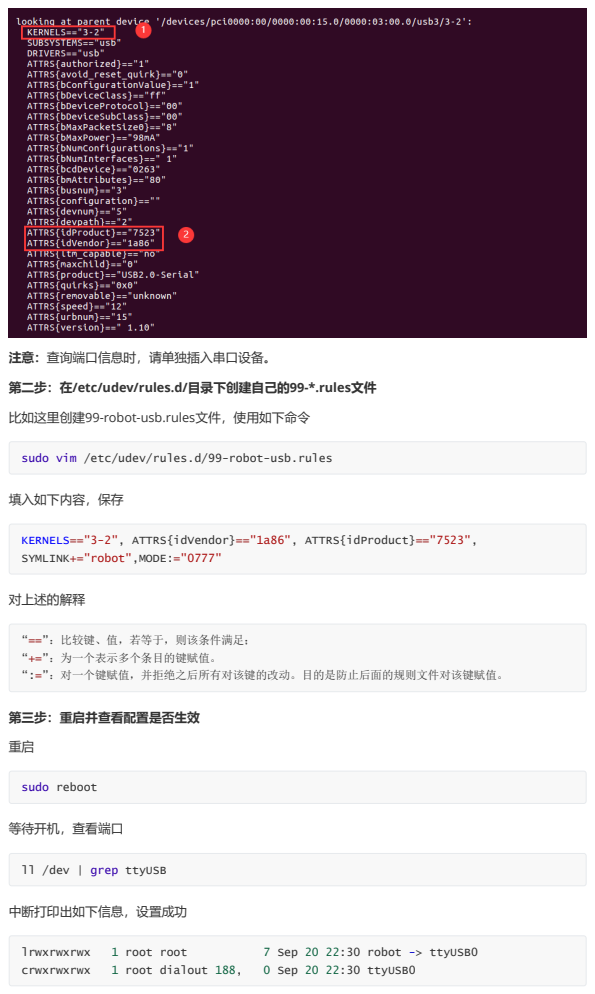
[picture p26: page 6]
填入如下内容，保存; 对上述的解释; 第三步：重启并查看配置是否生效; 等待开机，查看端口; 中断打印出如下信息，设置成功; sudo reboot; lrwxrwxrwx; 1 root root; 7 Sep 20 22:30 robot -> ttyUSB0; crwxrwxrwx; 1 root dialout 188,; 0 Sep 20 22:30 ttyUSB0

注意：查询端口信息时，请单独插入串口设备。
第二步：在/etc/udev/rules.d/目录下创建自己的99-*.rules文件
比如这里创建99-robot-usb.rules文件，使用如下命令

sudo vim /etc/udev/rules.d/99-robot-usb.rules

KERNELS=="3-2", ATTRS{idVendor}=="1a86", ATTRS{idProduct}=="7523",
SYMLINK+="robot",MODE:="0777"

“==”：比较键、值，若等于，则该条件满足；
“+=”：为一个表示多个条目的键赋值。
“:=”：对一个键赋值，并拒绝之后所有对该键的改动。目的是防止后面的规则文件对该键赋值。

ll /dev | grep ttyUSB
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

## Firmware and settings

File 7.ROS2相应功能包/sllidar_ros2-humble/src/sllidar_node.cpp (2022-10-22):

/*
 *  SLLIDAR ROS2 NODE
 *
 *  Copyright (c) 2009 - 2014 RoboPeak Team
 *  http://www.robopeak.com
 *  Copyright (c) 2014 - 2022 Shanghai Slamtec Co., Ltd.
 *  http://www.slamtec.com
 *
 */
/*
 * Redistribution and use in source and binary forms, with or without
 * modification, are permitted provided that the following conditions are met:
 *
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
 * THIS SOFTWARE IS PROVIDED BY THE COPYRIGHT HOLDERS AND CONTRIBUTORS "AS IS"
 * AND ANY EXPRESS OR IMPLIED WARRANTIES, INCLUDING, BUT NOT LIMITED TO,
 * THE IMPLIED WARRANTIES OF MERCHANTABILITY AND FITNESS FOR A PARTICULAR
 * PURPOSE ARE DISCLAIMED. IN NO EVENT SHALL THE COPYRIGHT HOLDER OR
 * CONTRIBUTORS BE LIABLE FOR ANY DIRECT, INDIRECT, INCIDENTAL, SPECIAL,
 * EXEMPLARY, OR CONSEQUENTIAL DAMAGES (INCLUDING, BUT NOT LIMITED TO,
 * PROCUREMENT OF SUBSTITUTE GOODS OR SERVICES; LOSS OF USE, DATA, OR PROFITS;
 * OR BUSINESS INTERRUPTION) HOWEVER CAUSED AND ON ANY THEORY OF LIABILITY,
 * WHETHER IN CONTRACT, STRICT LIABILITY, OR TORT (INCLUDING NEGLIGENCE OR
 * OTHERWISE) ARISING IN ANY WAY OUT OF THE USE OF THIS SOFTWARE,
 * EVEN IF ADVISED OF THE POSSIBILITY OF SUCH DAMAGE.
 *
 */

#include <rclcpp/rclcpp.hpp>
#include <sensor_msgs/msg/laser_scan.hpp>
#include <std_srvs/srv/empty.hpp>
#include "sl_lidar.h"
#include "math.h"

#include <signal.h>

#ifndef _countof
#define _countof(_Array) (int)(sizeof(_Array) / sizeof(_Array[0]))
#endif

#define DEG2RAD(x) ((x)*M_PI/180.)

#define ROS2VERSION "1.0.1"

using namespace sl;

bool need_exit = false;

class SLlidarNode : public rclcpp::Node
{
  public:
    SLlidarNode()
    : Node("sllidar_node")
    {

      scan_pub = this->create_publisher<sensor_msgs::msg::LaserScan>("scan", rclcpp::QoS(rclcpp::KeepLast(10)));
      
    }

  private:    
    void init_param()
    {
        this->declare_parameter<std::string>("channel_type", "serial");
        this->declare_parameter<std::string>("tcp_ip","192.168.0.7");
        this->declare_parameter<int>("tcp_port", 20108);
        this->declare_parameter<std::string>("udp_ip", "192.168.11.2");
        this->declare_parameter<int>("udp_port",8089);
        this->declare_parameter<std::string>("serial_port", "/dev/rplidars2");
        this->declare_parameter<int>("serial_baudrate", 1000000);
        this->declare_parameter<std::string>("frame_id", "laser_link");
        this->declare_parameter<bool>("inverted", false);
        this->declare_parameter<bool>("angle_compensate", false);
        this->declare_parameter<std::string>("scan_mode","Standard");
        this->declare_parameter<float>("scan_frequency", 20.0);

        this->get_parameter_or<std::string>("channel_type", channel_type, "serial");
        this->get_parameter_or<std::string>("tcp_ip", tcp_ip, "192.168.0.7"); 
        this->get_parameter_or<int>("tcp_port", tcp_port, 20108);
        this->get_parameter_or<std::string>("udp_ip", udp_ip, "192.168.11.2"); 
        this->get_parameter_or<int>("udp_port", udp_port, 8089);
        this->get_parameter_or<std::string>("serial_port", serial_port, "/dev/rplidars2"); 
        this->get_parameter_or<int>("serial_baudrate", serial_baudrate, 1000000);//ros run for A1 A2, change to 256000 if A3
        this->get_parameter_or<std::string>("frame_id", frame_id, "laser_link");
        this->get_parameter_or<bool>("inverted", inverted, false);
        this->get_parameter_or<bool>("angle_compensate", angle_compensate, false);
        this->get_parameter_or<std::string>("scan_mode", scan_mode, std::string());
        this->get_parameter_or<float>("scan_frequency", scan_frequency, 20.0);
    }

    bool getSLLIDARDeviceInfo(ILidarDriver * drv)
    {
        sl_result     op_result;
        sl_lidar_response_device_info_t devinfo;

        op_result = drv->getDeviceInfo(devinfo);
        if (SL_IS_FAIL(op_result)) {
            if (op_result == SL_RESULT_OPERATION_TIMEOUT) {
                RCLCPP_ERROR(this->get_logger(),"Error, operation time out. SL_RESULT_OPERATION_TIMEOUT! ");
            } else {
                RCLCPP_ERROR(this->get_logger(),"Error, unexpected error, code: %x",op_result);
            }
            return false;
        }

        // print out the device serial number, firmware and hardware version number..
        char sn_str[37] = {'\0'}; 
        for (int pos = 0; pos < 16 ;++pos) {
            sprintf(sn_str + (pos * 2),"%02X", devinfo.serialnum[pos]);
        }
        RCLCPP_INFO(this->get_logger(),"SLLidar S/N: %s",sn_str);
        RCLCPP_INFO(this->get_logger(),"Firmware Ver: %d.%02d",devinfo.firmware_version>>8, devinfo.firmware_version & 0xFF);
        RCLCPP_INFO(this->get_logger(),"Hardware Rev: %d",(int)devinfo.hardware_version);
        return true;
    }

    bool checkSLLIDARHealth(ILidarDriver * drv)
    {
        sl_result     op_result;
        sl_lidar_response_device_health_t healthinfo;
        op_result = drv->getHealth(healthinfo);
        if (SL_IS_OK(op_result)) { 
            RCLCPP_INFO(this->get_logger(),"SLLidar health status : %d", healthinfo.status);
            switch (healthinfo.status) {
                case SL_LIDAR_STATUS_OK:
                    RCLCPP_INFO(this->get_logger(),"SLLidar health status : OK.");
                    return true;
                case SL_LIDAR_STATUS_WARNING:
                    RCLCPP_INFO(this->get_logger(),"SLLidar health status : Warning.");
                    return true;
                case SL_LIDAR_STATUS_ERROR:
                    RCLCPP_ERROR(this->get_logger(),"Error, SLLidar internal error detected. Please reboot the device to retry.");
                    return false;
            }
        } else {
            RCLCPP_ERROR(this->get_logger(),"Error, cannot retrieve SLLidar health code: %x", op_result);
            return false;
        }
    }

    bool stop_motor(const std::shared_ptr<std_srvs::srv::Empty::Request> req,
                    std::shared_ptr<std_srvs::srv::Empty::Response> res)
    {
        (void)req;
        (void)res;

        if(!drv)
            return false;

        RCLCPP_DEBUG(this->get_logger(),"Stop motor");
        drv->setMotorSpeed(0);
        return true;
    }

    bool start_motor(const std::shared_ptr<std_srvs::srv::Empty::Request> req,
                    std::shared_ptr<std_srvs::srv::Empty::Response> res)
    {
        (void)req;
        (void)res;

        if(!drv)
           return false;
        if(drv->isConnected())
        {
            RCLCPP_DEBUG(this->get_logger(),"Start motor");
            sl_result ans=drv->setMotorSpeed();
            if (SL_IS_FAIL(ans)) {
                RCLCPP_WARN(this->get_logger(), "Failed to start motor: %08x", ans);
                return false;
            }
        
            ans=drv->startScan(0,1);
            if (SL_IS_FAIL(ans)) {
                RCLCPP_WARN(this->get_logger(), "Failed to start scan: %08x", ans);
            }
        } else {
            RCLCPP_INFO(this->get_logger(),"lost connection");
            return false;
        }

        return true;
    }

    static float getAngle(const sl_lidar_response_measurement_node_hq_t& node)
    {
        return node.angle_z_q14 * 90.f / 16384.f;
    }

    void publish_scan(rclcpp::Publisher<sensor_msgs::msg::LaserScan>::SharedPtr& pub,
                  sl_lidar_response_measurement_node_hq_t *nodes,
                  size_t node_count, rclcpp::Time start,
                  double scan_time, bool inverted,
                  float angle_min, float angle_max,
                  float max_distance,
                  std::string frame_id)
    {
        static int scan_count = 0;
        auto scan_msg = std::make_shared<sensor_msgs::msg::LaserScan>();

        scan_msg->header.stamp = start;
        scan_msg->header.frame_id = frame_id;
        scan_count++;

        bool reversed = (angle_max > angle_min);
        if ( reversed ) {
            scan_msg->angle_min =  M_PI - angle_max;
            scan_msg->angle_max =  M_PI - angle_min;
        } else {
            scan_msg->angle_min =  M_PI - angle_min;
            scan_msg->angle_max =  M_PI - angle_max;
        }
        scan_msg->angle_increment = (scan_msg->angle_max - scan_msg->angle_min) / (double)(node_count-1);

        scan_msg->scan_time = scan_time;
        scan_msg->time_increment = scan_time / (double)(node_count-1);
        scan_msg->range_min = 0.15;
        scan_msg->range_max = max_distance;//8.0;

        scan_msg->intensities.resize(node_count);
        scan_msg->ranges.resize(node_count);
        bool reverse_data = (!inverted && reversed) || (inverted && !reversed);
        if (!reverse_data) {
            for (size_t i = 0; i < node_count; i++) {
                float read_value = (float) nodes[i].dist_mm_q2/4.0f/1000;
                if (read_value == 0.0)
                    scan_msg->ranges[i] = std::numeric_limits<float>::infinity();
                else
                    scan_msg->ranges[i] = read_value;
                scan_msg->intensities[i] = (float) (nodes[i].quality >> 2);
            }
        } else {
            for (size_t i = 0; i < node_count; i++) {
                float read_value = (float)nodes[i].dist_mm_q2/4.0f/1000;
                if (read_value == 0.0)
                    scan_msg->ranges[node_count-1-i] = std::numeric_limits<float>::infinity();
                else
                    scan_msg->ranges[node_count-1-i] = read_value;
                scan_msg->intensities[node_count-1-i] = (float) (nodes[i].quality >> 2);
            }
        }

        pub->publish(*scan_msg);
    }
public:    
    int work_loop()
    {        
        init_param();
        int ver_major = SL_LIDAR_SDK_VERSION_MAJOR;
        int ver_minor = SL_LIDAR_SDK_VERSION_MINOR;
        int ver_patch = SL_LIDAR_SDK_VERSION_PATCH;
        RCLCPP_INFO(this->get_logger(),"SLLidar running on ROS2 package SLLidar.ROS2 SDK Version:" ROS2VERSION ", SLLIDAR SDK Version:%d.%d.%d",ver_major,ver_minor,ver_patch);
    
        sl_result     op_result;

        // create the driver instance
        drv = *createLidarDriver();
        IChannel* _channel;
        if(channel_type == "tcp"){
            _channel = *createTcpChannel(tcp_ip, tcp_port);
        }
        else if(channel_type == "udp"){
            _channel = *createUdpChannel(udp_ip, udp_port);
        }
        else{
            _channel = *createSerialPortChannel(serial_port, serial_baudrate);
        }
        if (SL_IS_FAIL((drv)->connect(_channel))) {
            if(channel_type == "tcp"){
                RCLCPP_ERROR(this->get_logger(),"Error, cannot connect to the ip addr  %s with the tcp port %s.",tcp_ip.c_str(),std::to_string(tcp_port).c_str());
            }
            else if(channel_type == "udp"){
                RCLCPP_ERROR(this->get_logger(),"Error, cannot connect to the ip addr  %s with the udp port %s.",udp_ip.c_str(),std::to_string(udp_port).c_str());
            }
            else{
                RCLCPP_ERROR(this->get_logger(),"Error, cannot bind to the specified serial port %s.",serial_port.c_str());            
            }
            delete drv;
            return -1;
        }
        
        // get sllidar device info
        if (!getSLLIDARDeviceInfo(drv)) {
            return -1;
        }

        // check health...
        if (!checkSLLIDARHealth(drv)) {
            return -1;
        }

        stop_motor_service = this->create_service<std_srvs::srv::Empty>("stop_motor",  
                                std::bind(&SLlidarNode::stop_motor,this,std::placeholders::_1,std::placeholders::_2));
        start_motor_service = this->create_service<std_srvs::srv::Empty>("start_motor", 
                                std::bind(&SLlidarNode::start_motor,this,std::placeholders::_1,std::placeholders::_2));

        drv->setMotorSpeed();

        LidarScanMode current_scan_mode;
        if (scan_mode.empty()) {
            op_result = drv->startScan(false /* not force scan */, true /* use typical scan mode */, 0, &current_scan_mode);
        } else {
            std::vector<LidarScanMode> allSupportedScanModes;
            op_result = drv->getAllSupportedScanModes(allSupportedScanModes);

            if (SL_IS_OK(op_result)) {
                sl_u16 selectedScanMode = sl_u16(-1);
                for (std::vector<LidarScanMode>::iterator iter = allSupportedScanModes.begin(); iter != allSupportedScanModes.end(); iter++) {
                    if (iter->scan_mode == scan_mode) {
                        selectedScanMode = iter->id;
                        break;
                    }
                }

                if (selectedScanMode == sl_u16(-1)) {
                    RCLCPP_ERROR(this->get_logger(),"scan mode `%s' is not supported by lidar, supported modes:", scan_mode.c_str());
                    for (std::vector<LidarScanMode>::iterator iter = allSupportedScanModes.begin(); iter != allSupportedScanModes.end(); iter++) {
                        RCLCPP_ERROR(this->get_logger(),"\t%s: max_distance: %.1f m, Point number: %.1fK",  iter->scan_mode,
                                iter->max_distance, (1000/iter->us_per_sample));
                    }
                    op_result = SL_RESULT_OPERATION_FAIL;
                } else {
                    op_result = drv->startScanExpress(false /* not force scan */, selectedScanMode, 0, &current_scan_mode);
                }
            }
        }

        if(SL_IS_OK(op_result))
        {
            //default frequent is 10 hz (by motor pwm value),  current_scan_mode.us_per_sample is the number of scan point per us
            int points_per_circle = (int)(1000*1000/current_scan_mode.us_per_sample/scan_frequency);
            angle_compensate_multiple = points_per_circle/360.0  + 1;
            if(angle_compensate_multiple < 1) 
            angle_compensate_multiple = 1.0;
            max_distance = (float)current_scan_mode.max_distance;
            RCLCPP_INFO(this->get_logger(),"current scan mode: %s, sample rate: %d Khz, max_distance: %.1f m, scan frequency:%.1f Hz, ", 
                                current_scan_mode.scan_mode,(int)(1000/current_scan_mode.us_per_sample+0.5),max_distance, scan_frequency);
        }
        else
        {
            RCLCPP_ERROR(this->get_logger(),"Can not start scan: %08x!", op_result);
        }

        rclcpp::Time start_scan_time;
        rclcpp::Time end_scan_time;
        double scan_duration;
        while (rclcpp::ok() && !need_exit) {
            sl_lidar_response_measurement_node_hq_t nodes[8192];
            size_t   count = _countof(nodes);

            start_scan_time = this->now();
            op_result = drv->grabScanDataHq(nodes, count);
            end_scan_time = this->now();
            scan_duration = (end_scan_time - start_scan_time).seconds();

            if (op_result == SL_RESULT_OK) {
                op_result = drv->ascendScanData(nodes, count);
                float angle_min = DEG2RAD(0.0f);
                float angle_max = DEG2RAD(359.0f);
                if (op_result == SL_RESULT_OK) {
                    if (angle_compensate) {
                        //const int angle_compensate_multiple = 1;
                        const int angle_compensate_nodes_count = 360*angle_compensate_multiple;
                        int angle_compensate_offset = 0;
                        auto angle_compensate_nodes = new sl_lidar_response_measurement_node_hq_t[angle_compensate_nodes_count];
                        memset(angle_compensate_nodes, 0, angle_compensate_nodes_count*sizeof(sl_lidar_response_measurement_node_hq_t));

                        size_t i = 0, j = 0;
                        for( ; i < count; i++ ) {
                            if (nodes[i].dist_mm_q2 != 0) {
                                float angle = getAngle(nodes[i]);
                                int angle_value = (int)(angle * angle_compensate_multiple);
                                if ((angle_value - angle_compensate_offset) < 0) angle_compensate_offset = angle_value;
                                for (j = 0; j < angle_compensate_multiple; j++) {
                                    int angle_compensate_nodes_index = angle_value-angle_compensate_offset + j;
                                    if(angle_compensate_nodes_index >= angle_compensate_nodes_count)
                                        angle_compensate_nodes_index = angle_compensate_nodes_count - 1;
                                    angle_compensate_nodes[angle_compensate_nodes_index] = nodes[i];
                                }
                            }
                        }
    
                        publish_scan(scan_pub, angle_compensate_nodes, angle_compensate_nodes_count,
                                start_scan_time, scan_duration, inverted,
                                angle_min, angle_max, max_distance,
                                frame_id);

                        if (angle_compensate_nodes) {
                            delete[] angle_compensate_nodes;
                            angle_compensate_nodes = nullptr;
                        }
                    } else {
                        int start_node = 0, end_node = 0;
                        int i = 0;
                        // find the first valid node and last valid node
                        while (nodes[i++].dist_mm_q2 == 0);
                        start_node = i-1;
                        i = count -1;
                        while (nodes[i--].dist_mm_q2 == 0);
                        end_node = i+1;

                        angle_min = DEG2RAD(getAngle(nodes[start_node]));
                        angle_max = DEG2RAD(getAngle(nodes[end_node]));

                        publish_scan(scan_pub, &nodes[start_node], end_node-start_node +1,
                                start_scan_time, scan_duration, inverted,
                                angle_min, angle_max, max_distance,
                                frame_id);
                    }
                } else if (op_result == SL_RESULT_OPERATION_FAIL) {
                    // All the data is invalid, just publish them
                    float angle_min = DEG2RAD(0.0f);
                    float angle_max = DEG2RAD(359.0f);
                    publish_scan(scan_pub, nodes, count,
                                start_scan_time, scan_duration, inverted,
                                angle_min, angle_max, max_distance,
                                frame_id);
                }
            }

            rclcpp::spin_some(shared_from_this());
        }

        // done!
        drv->setMotorSpeed(0);
        drv->stop();
        RCLCPP_INFO(this->get_logger(),"Stop motor");

        return 0;
    }


  private:
    rclcpp::Publisher<sensor_msgs::msg::LaserScan>::SharedPtr scan_pub;
    rclcpp::Service<std_srvs::srv::Empty>::SharedPtr start_motor_service;
    rclcpp::Service<std_srvs::srv::Empty>::SharedPtr stop_motor_service;

    std::string channel_type;
    std::string tcp_ip;
    std::string udp_ip;
    std::string serial_port;
    int tcp_port = 20108;
    int udp_port = 8089;
    int serial_baudrate = 115200;
    std::string frame_id;
    bool inverted = false;
    bool angle_compensate = true;
    float max_distance = 8.0;
    size_t angle_compensate_multiple = 1;//it stand of angle compensate at per 1 degree
    std::string scan_mode;
    float scan_frequency;

    ILidarDriver * drv;    
};

void ExitHandler(int sig)
{
    (void)sig;
    need_exit = true;
}


int main(int argc, char * argv[])
{
  rclcpp::init(argc, argv);  
  auto sllidar_node = std::make_shared<SLlidarNode>();
  signal(SIGINT,ExitHandler);
  int ret = sllidar_node->work_loop();
  rclcpp::shutdown();
  return ret;
}

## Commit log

2022-10-22 小白学移动机器人-第一次提交
    [BOM_Board1_PCB_2022-10-09.xlsx, PickAndPlace_PCB_2022-10-09.xlsx, left_back_wheel_1.stl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]
2022-10-23 修复底层驱动程序上传为空的情况
